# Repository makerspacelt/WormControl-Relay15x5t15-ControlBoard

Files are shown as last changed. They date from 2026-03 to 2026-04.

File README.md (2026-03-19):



---
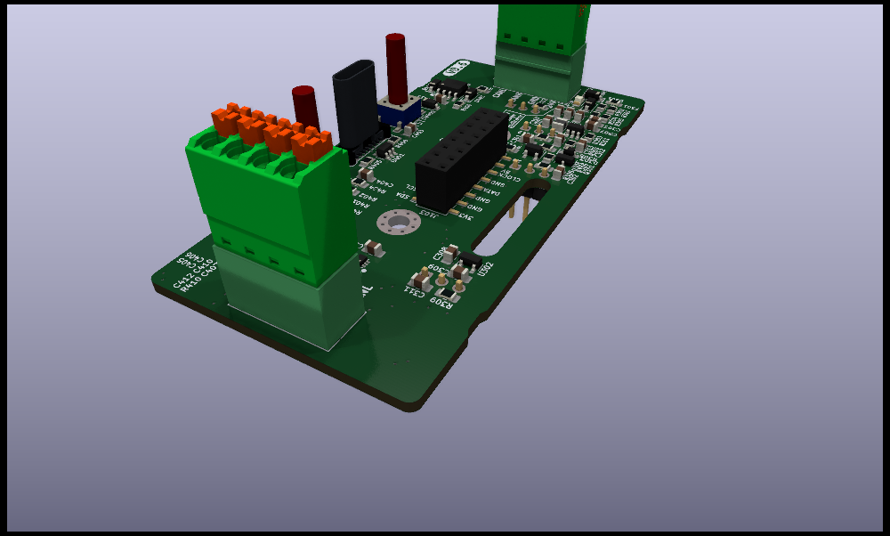
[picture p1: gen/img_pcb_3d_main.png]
PCB 3d main


WormControl Relay Control boards

Dev NOTE: before commit, run `./kibot.sh` to regenerate documentation, bom, gerbers and other assets.

* [schematics.pdf](gen/schematics.pdf)
* [pcb.pdf with dimensions](gen/pcb.pdf)
* [ibom.html](gen/single/ibom.html)

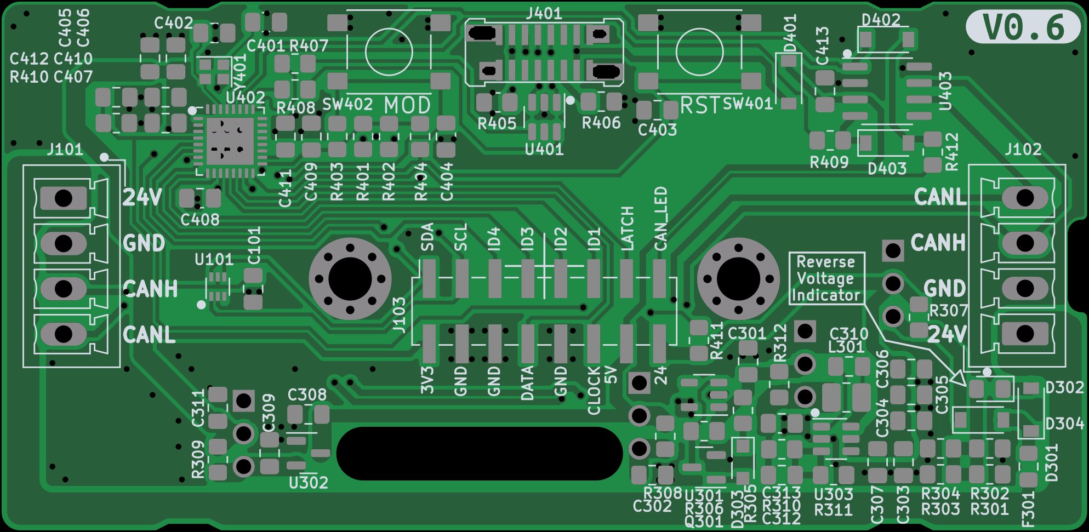
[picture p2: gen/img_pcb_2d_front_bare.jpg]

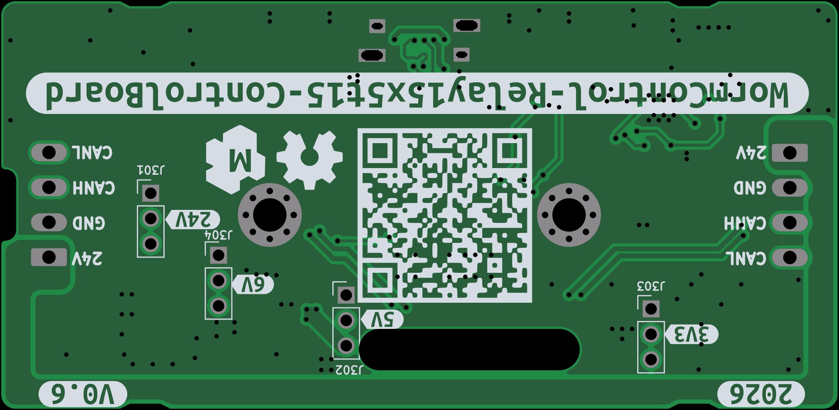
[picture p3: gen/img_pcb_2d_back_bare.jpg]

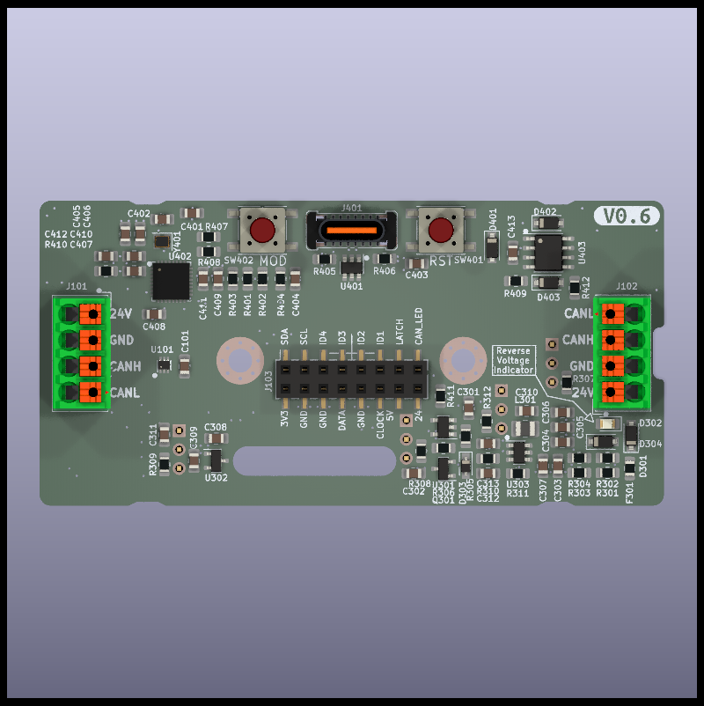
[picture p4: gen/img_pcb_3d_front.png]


---

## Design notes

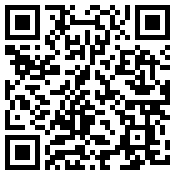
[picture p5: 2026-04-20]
gen/qr_link.png

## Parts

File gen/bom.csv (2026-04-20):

Row | Description | Part | References | Value | Footprint | Quantity Per PCB | Status | Datasheet | lcsc# | jlc-part-type | alt#
1 | Heatsink | Heatsink | BOM101,BOM102 | 1x4 screw plug |  | 2 |  | https://www.lcsc.com/datasheet/lcsc_datasheet_2309070925_DEGSON-15EDGKN-3-5-04P-14-00A-H_C7603442.pdf | C7603442 | E
2 | Unpolarized capacitor | C | C401,C402 | 10p | C_0805_2012Metric_Pad1.18x1.45mm_HandSolder | 2 |  | https://www.lcsc.com/datasheet/lcsc_datasheet_2304140030_Samsung-Electro-Mechanics-CL10C100JB8NNNC_C1634.pdf | C1634 | B
3 | Unpolarized capacitor | C | C312 | 100p | C_0805_2012Metric_Pad1.18x1.45mm_HandSolder | 1 |  | https://www.lcsc.com/datasheet/lcsc_datasheet_2304140030_Samsung-Electro-Mechanics-CL21C101JBANNNC_C1790.pdf | C1790 | B
4 | Unpolarized capacitor | C | C101,C307,C310,C403,C404,C407,C408,C409,C410,C411,C412,C413 | 100n | C_0805_2012Metric_Pad1.18x1.45mm_HandSolder | 12 |  | https://www.lcsc.com/datasheet/lcsc_datasheet_2304140030_Samsung-Electro-Mechanics-CL21B104KCFNNNE_C28233.pdf | C28233 | B
5 | Unpolarized capacitor | C | C406 | 1u | C_0805_2012Metric_Pad1.18x1.45mm_HandSolder | 1 |  | https://www.lcsc.com/datasheet/lcsc_datasheet_2304140030_Samsung-Electro-Mechanics-CL21B105KBFNNNE_C28323.pdf | C28323 | B
6 | Unpolarized capacitor | C | C301,C303,C304,C305,C306,C313 | 10u/50v | C_0805_2012Metric_Pad1.18x1.45mm_HandSolder | 6 |  | https://www.lcsc.com/datasheet/lcsc_datasheet_2411041759_Murata-Electronics-GRM21BR61H106KE43L_C440198.pdf | C440198 | B
7 | Unpolarized capacitor | C | C302,C308,C405 | 22u/25v | C_0805_2012Metric_Pad1.18x1.45mm_HandSolder | 3 |  | https://www.lcsc.com/datasheet/lcsc_datasheet_2304140030_Samsung-Electro-Mechanics-CL21A226MAQNNNE_C45783.pdf | C45783 | B
8 | Unpolarized capacitor | C | C309,C311 | 47u/6V3 | C_0805_2012Metric_Pad1.18x1.45mm_HandSolder | 2 |  | https://www.lcsc.com/datasheet/lcsc_datasheet_2304140030_Samsung-Electro-Mechanics-CL21A226MAQNNNE_C45783.pdf | C16780 | B
9 | Zener diode | D_Zener | D303 | 6V8 | D_SOD-323_HandSoldering | 1 |  | https://www.lcsc.com/datasheet/C123062.pdf | C123062 | E
10 | Schottky diode | D_Schottky | D301,D304,D401,D402,D403 | B5819W | D_SOD-123 | 5 |  | https://www.lcsc.com/datasheet/lcsc_datasheet_2304140030_Jiangsu-Changjing-Electronics-Technology-Co---Ltd--B5819W-SL_C8598.pdf | C8598 | B
11 | Light emitting diode | LED | D302 | BLUE | LED_0805_2012Metric_Pad1.15x1.40mm_HandSolder | 1 |  | https://jlcpcb.com/api/file/downloadByFileSystemAccessId/8550724011370958848 | C2297 | B
12 | Resettable fuse, polymeric positive temperature coefficient | Polyfuse | F301 | 250mA | Fuse_0805_2012Metric_Pad1.15x1.40mm_HandSolder | 1 |  | https://wmsc.lcsc.com/wmsc/upload/file/pdf/v2/lcsc/2404081622_BHFUSE-BSMD0805-025-33V_C22378353.pdf | C22378353 | E
13 | Generic connector, single row, 01x03, script generated (kicad-library-utils/schlib/autogen/connector/) | Conn_01x03 | J301,J302,J303,J304 | 24V | PinHeader_1x03_P2.54mm_Vertical | 4 |  | ~ |  | -
14 | Generic screw terminal, single row, 01x04, script generated (kicad-library-utils/schlib/autogen/connector/) | Screw_Terminal_01x04 | J101,J102 | BUS | PhoenixContact_MCV_1,5_4-G-3.5_1x04_P3.50mm_Vertical | 2 |  | https://www.lcsc.com/datasheet/lcsc_datasheet_2304140030_Ningbo-Xinlaiya-Elec--XY2500V-F-3-5-4P_C880556.pdf | C880556 | E
15 | Generic connector, single row, 01x16, script generated (kicad-library-utils/schlib/autogen/connector/) | Conn_01x16 | J103 | Back | PinSocket_2x08_P2.54mm_Vertical_SMD | 1 |  | https://wmsc.lcsc.com/wmsc/upload/file/pdf/v2/lcsc/2306091018_HCTL-PM254-2-08-S-8-5_C3975153.pdf | C3975153 | E
16 | USB 2.0-only Type-C Receptacle connector | USB_C_Receptacle_USB2.0 | J401 | USB_C_Receptacle_USB2.0 | USB_C_Receptacle_G-Switch_GT-USB-7082G | 1 |  | https://www.lcsc.com/datasheet/lcsc_datasheet_2405271642_G-Switch-GT-USB-7082G_C22383836.pdf | C22383836 | E
17 | Inductor | L | L301 | 3.3uH | L_1008_2520Metric_Pad1.43x2.20mm_HandSolder | 1 |  | https://www.lcsc.com/datasheet/C5832373.pdf | C5832373 | E
18 | NPN transistor, base/emitter/collector | Q_NPN_BEC | Q301 | MMBT3904 | SOT-23 | 1 |  | https://www.lcsc.com/datasheet/C20526.pdf | C20526 | B
19 | Resistor | R | R307,R308,R309,R312 | 0R1 | R_0805_2012Metric_Pad1.20x1.40mm_HandSolder | 4 |  | https://www.lcsc.com/datasheet/lcsc_datasheet_2304140030_UNI-ROYAL-Uniroyal-Elec-0805W8F100LT5E_C127687.pdf | C127687 | E
20 | Resistor | R | R407,R408 | 22R | R_0805_2012Metric_Pad1.20x1.40mm_HandSolder | 2 |  | ~ | C17561 | B
21 | Resistor | R | R301,R302,R303,R304,R401,R402,R403,R404,R405,R406,R409,R410,R412 | 4k7 | R_0805_2012Metric_Pad1.20x1.40mm_HandSolder | 13 |  | ~ | C17673 | B
22 | Resistor | R | R305,R306 | 10k | R_0805_2012Metric_Pad1.20x1.40mm_HandSolder | 2 |  | ~ | C17414 | B
23 | Resistor | R | R311 | 22k | R_0805_2012Metric_Pad1.20x1.40mm_HandSolder | 1 |  | ~ | C17560 | B
24 | Resistor | R | R411 | 150k | R_0805_2012Metric_Pad1.20x1.40mm_HandSolder | 1 |  | ~ | C17470 | B
25 | Resistor | R | R310 | 200k | R_0805_2012Metric_Pad1.20x1.40mm_HandSolder | 1 |  | ~ | C17539 | B
26 | Push button switch, generic, two pins | SW_Push | SW401,SW402 | 15mm | SW_SPST_15 | 2 |  | https://www.lcsc.com/datasheet/lcsc_datasheet_2110120830_XKB-Connection-TS-1102S-C-V-B_C2885154.pdf | C2885154 | E
27 | 300mA Low Dropout Voltage Regulator, Fixed Output 3.3V, SOT-23 | APE8865N-33-HF-3 | U302 | JTD6206-3.3V | SOT-23 | 1 |  | https://www.lcsc.com/datasheet/C42443428.pdf | C5446 | B | C42443428
28 | 300mA Low Dropout Voltage Regulator, Fixed Output 0.9V, SOT-23-5 | TLV71209_SOT23-5 | U301 | LW6550A23E | SOT-23-5 | 1 |  | https://www.lcsc.com/datasheet/C20754712.pdf | C20754712 | E
29 | 1.2 A Simple Buck Regulator, 3-26V input, 1.5Mhz | AOZ1280CI | U303 | ME3121AM6G | SOT-23-6 | 1 |  | https://m.huazhoucn.com/upFiles/common/2022/12/ME3121_Series_E1.0.pdf | C2932938 | E
30 | Digital Temperature Sensor, +/- 3 °C, low-Power, SMBus, 12 bit, Two-Wire Serial Interface, SOT-563 | TMP102xxDRL | U101 | TMP102 | SOT-563 | 1 |  | https://www.ti.com/lit/ds/symlink/tmp102.pdf | C99269 | E
31 | Very low capacitance ESD protection diode, 2 data-line, SOT-23-6 | USBLC6-2SC6 | U401 | USBLC6-2SC6 | SOT-23-6 | 1 |  | https://www.lcsc.com/datasheet/lcsc_datasheet_2311091738_UMW-Youtai-Semiconductor-Co---Ltd--USBLC6-2SC6_C2687116.pdf | C2687116 | E
32 | High-Speed CAN Transceiver, standby mode, split pin, SOIC-8 | TJA1042T | U403 | XL1050 | SOIC-8_3.9x4.9mm_P1.27mm | 1 |  | https://www.lcsc.com/datasheet/lcsc_datasheet_2309141025_XINLUDA-XL1050_C609746.pdf | C609746 | E
33 | esp32-C3FH4X 4MB flash QFN32-1EP 5x5mm EP3.7x3.7mm | esp32-C3FH4X | U402 | esp32-C3FH4X | QFN-32-1EP_5x5mm_P0.5mm_EP3.65x3.65mm | 1 |  | https://www.espressif.com/sites/default/files/documentation/esp32-c3_datasheet_en.pdf | C2858491 | E
34 | Four pin crystal, GND on pins 2 and 4 | Crystal_GND24 | Y401 | 40MHz | Crystal_SMD_2016-4Pin_2.0x1.6mm | 1 |  | https://www.lcsc.com/datasheet/C20885029.pdf | C20885029 | E

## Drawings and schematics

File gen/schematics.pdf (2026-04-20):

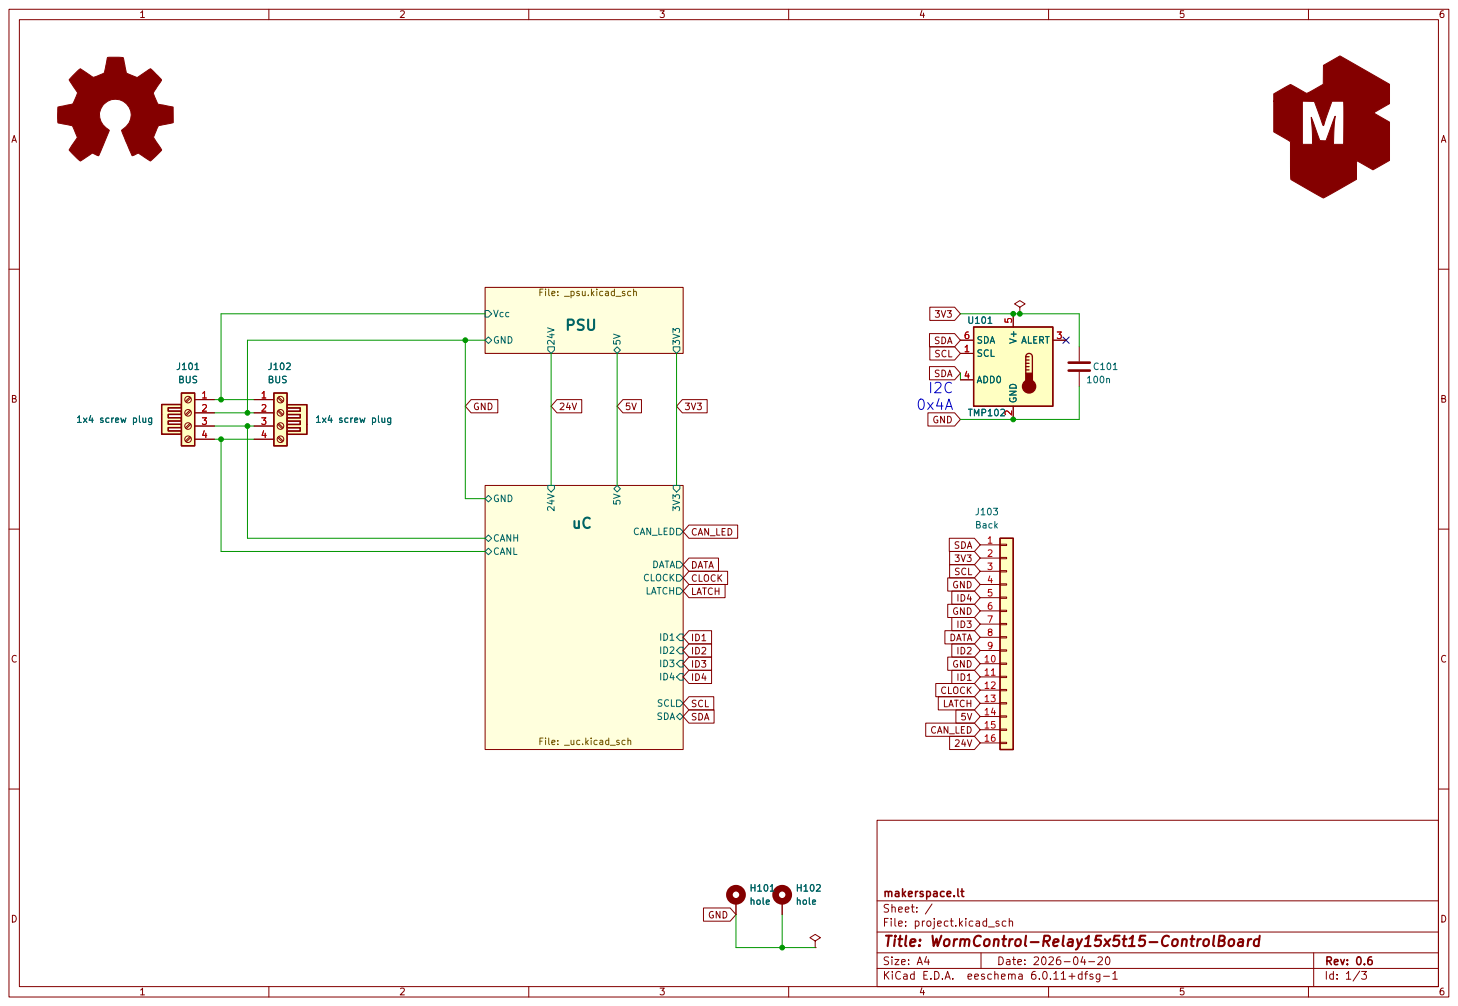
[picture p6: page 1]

Id: 1/3 Title: WormControl-Relay15x5t15-ControlBoard

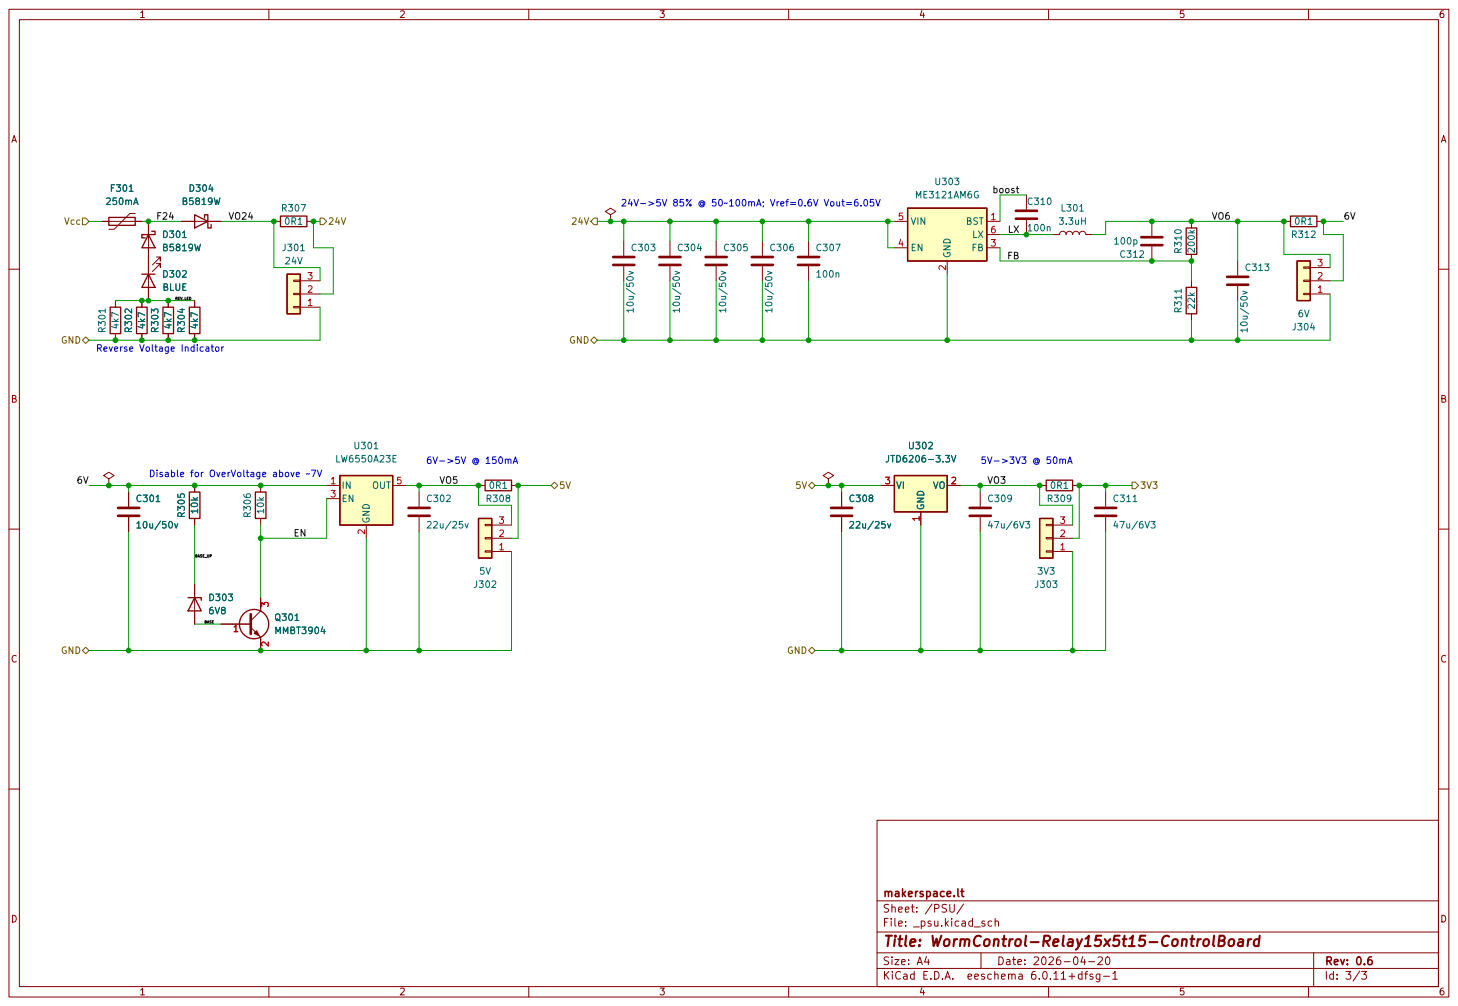
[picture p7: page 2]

boost Disable for OverVoltage above ~7V

Id: 3/3 Title: WormControl-Relay15x5t15-ControlBoard

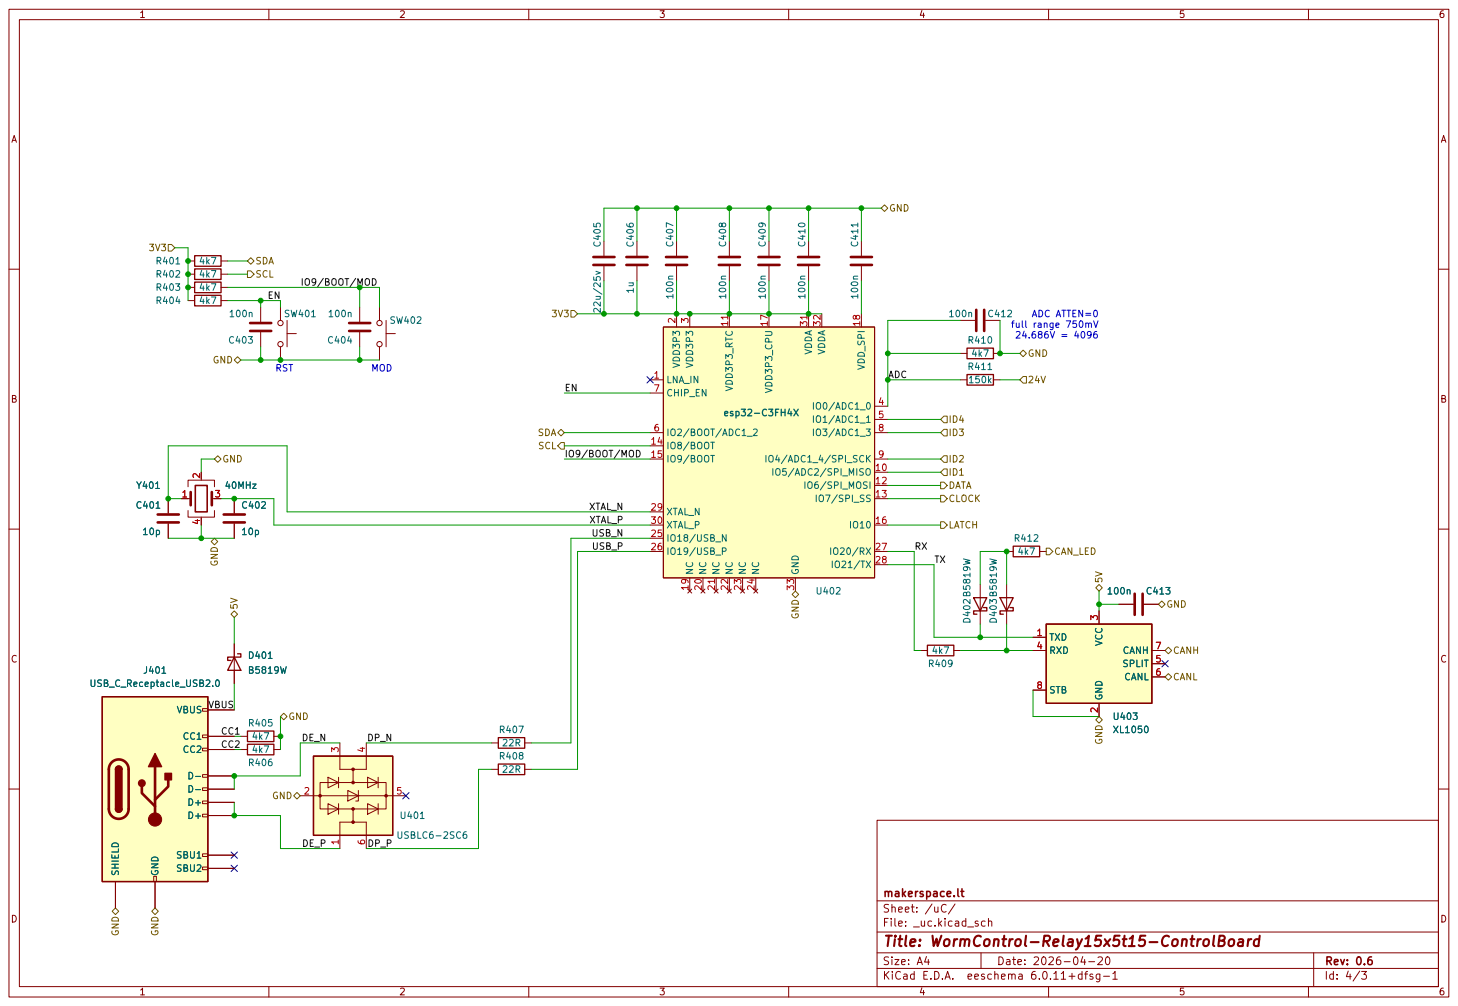
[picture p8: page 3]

File: _uc.kicad_sch Sheet: /uC/ makerspace.lt R407

Id: 4/3 Title: WormControl-Relay15x5t15-ControlBoard

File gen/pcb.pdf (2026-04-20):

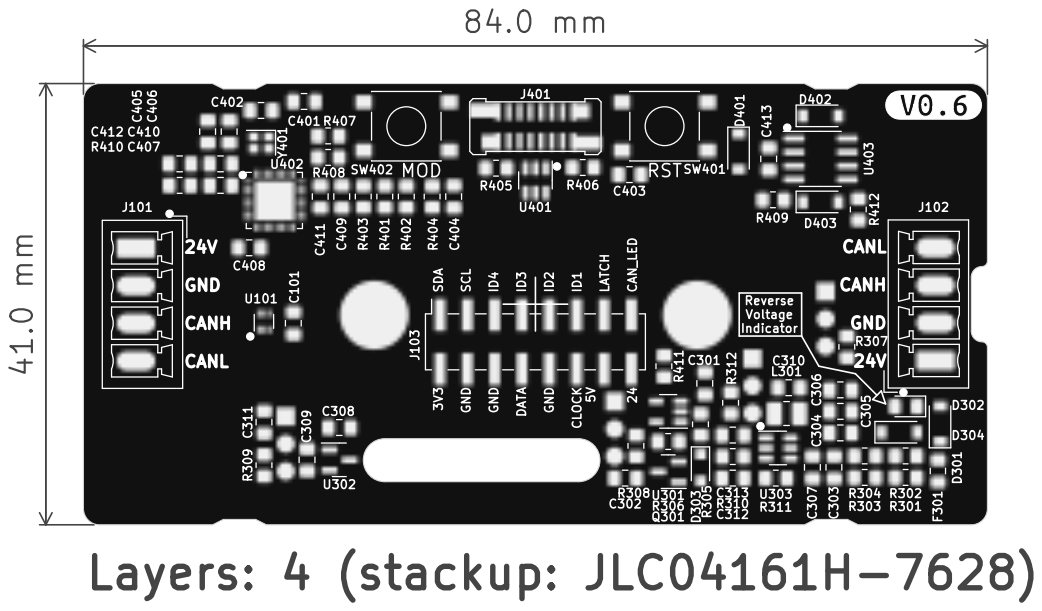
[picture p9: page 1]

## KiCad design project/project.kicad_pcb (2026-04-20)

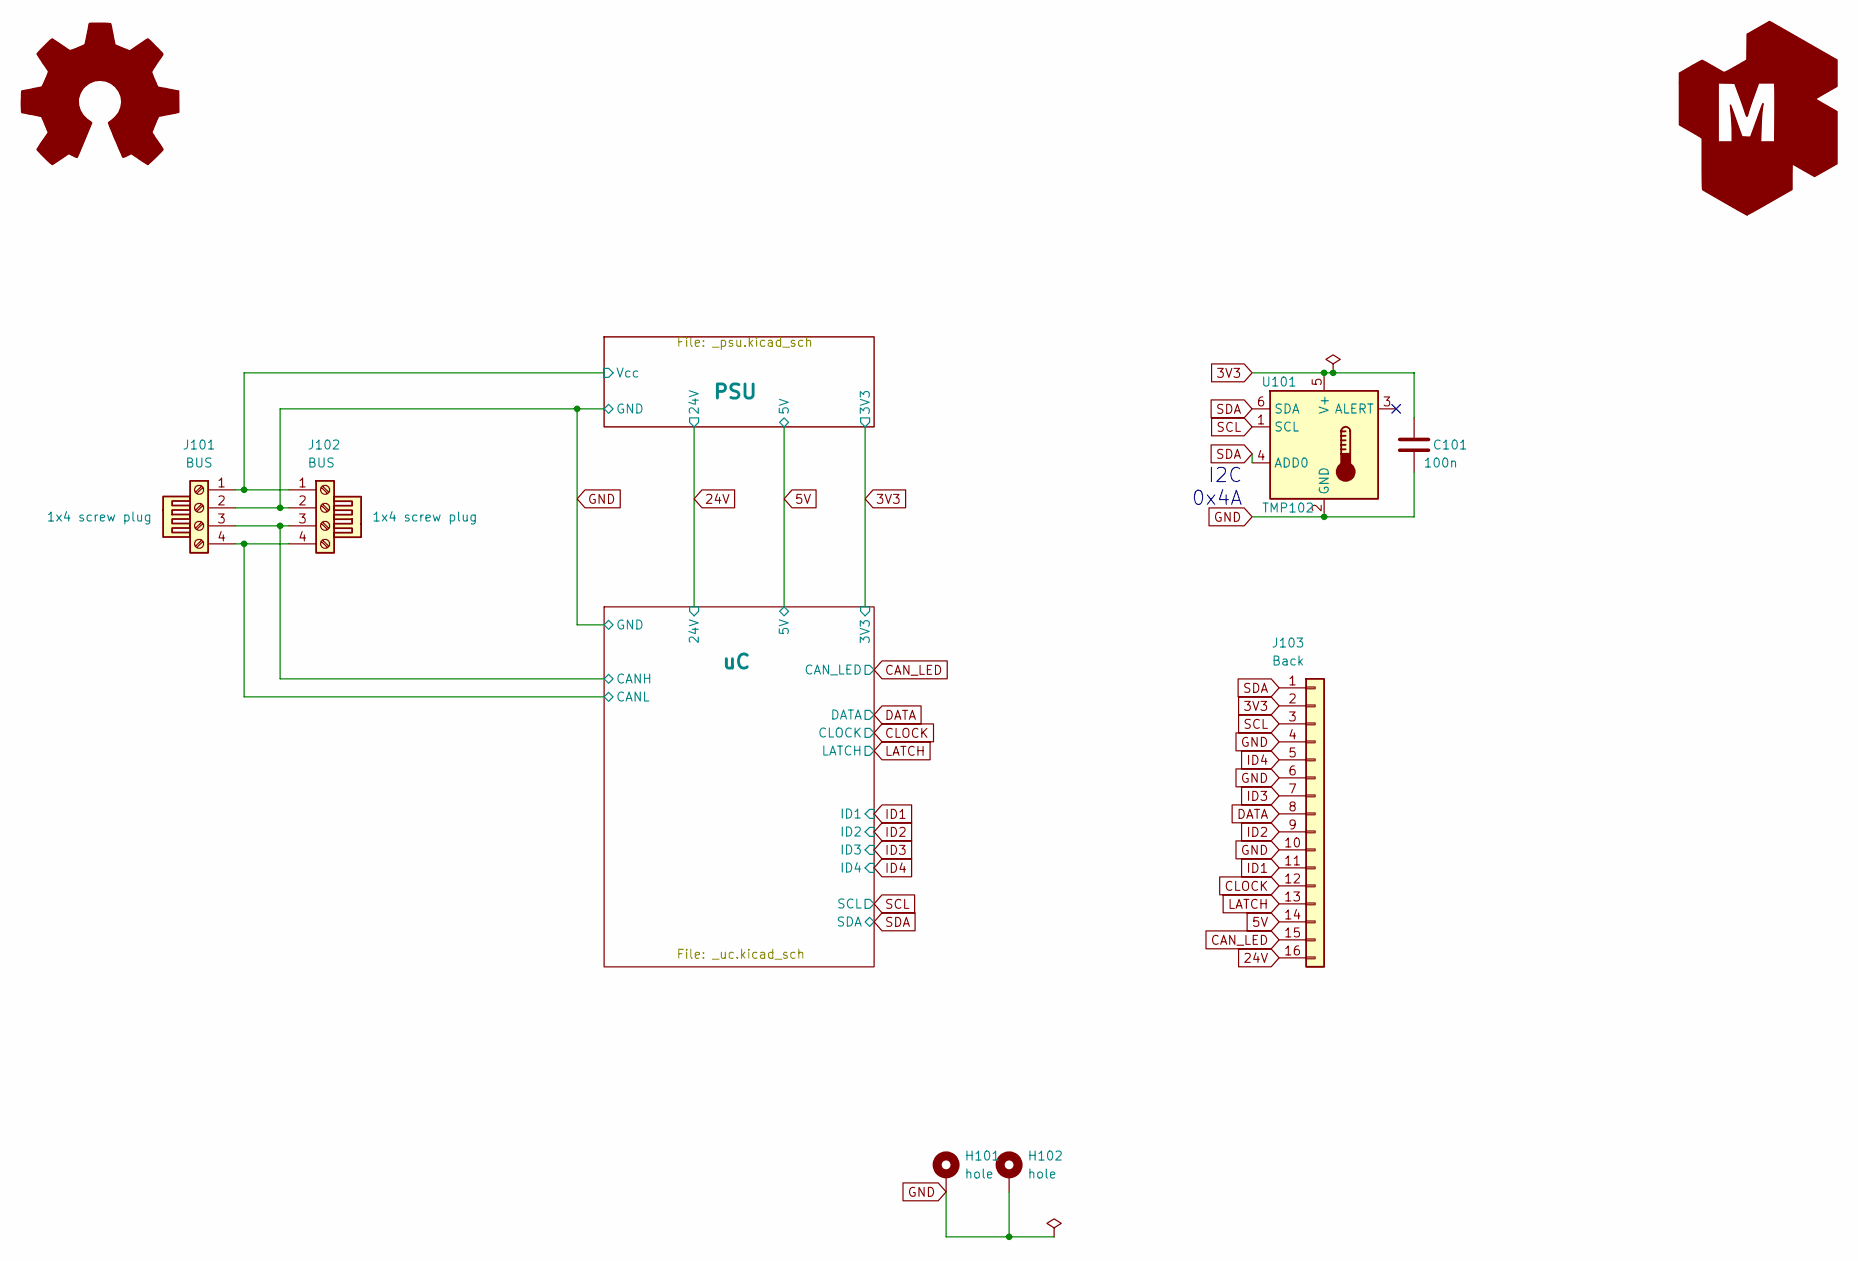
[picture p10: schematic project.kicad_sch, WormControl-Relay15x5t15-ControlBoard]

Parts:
BOM101, BOM102: 1x4 screw plug; jlc-part-type E
C101: 100n; C_0805_2012Metric_Pad1.18x1.45mm_HandSolder; jlc-part-type B
G101: Logo_Open_Hardware_Large; OSHW-Symbol_6.7x6mm_SilkScreen
G102: LOGO_KMS; logo_kms_small_silkscreen
H101, H102: hole; MountingHole_3.2mm_M3_Pad_Via
J101, J102: BUS; PhoenixContact_MCV_1,5_4-G-3.5_1x04_P3.50mm_Vertical; jlc-part-type E
J103: Back; PinSocket_2x08_P2.54mm_Vertical_SMD; lcsc# C3975153
U101: TMP102; SOT-563; jlc-part-type E

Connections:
3V3: C101.1, J103.2, U101.5 (V+); also elsewhere on the board
5V: J103.14; also elsewhere on the board
24V: J103.16; also elsewhere on the board
/PSU/Vcc: J101.1, J102.1; also elsewhere on the board
/uC/CANH: J101.3, J102.3; also elsewhere on the board
/uC/CANL: J101.4, J102.4; also elsewhere on the board
CAN_LED: J103.15; also elsewhere on the board
CLOCK: J103.12; also elsewhere on the board
DATA: J103.8; also elsewhere on the board
GND: C101.2, H101.1, H102.1, J101.2, J102.2, J103.4, J103.6, J103.10, U101.2 (GND); also elsewhere on the board
ID1: J103.11; also elsewhere on the board
ID2: J103.9; also elsewhere on the board
ID3: J103.7; also elsewhere on the board
ID4: J103.5; also elsewhere on the board
LATCH: J103.13; also elsewhere on the board
SCL: J103.3, U101.1 (SCL); also elsewhere on the board
SDA: J103.1, U101.4 (ADD0), U101.6 (SDA); also elsewhere on the board

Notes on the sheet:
I2C 0x4A

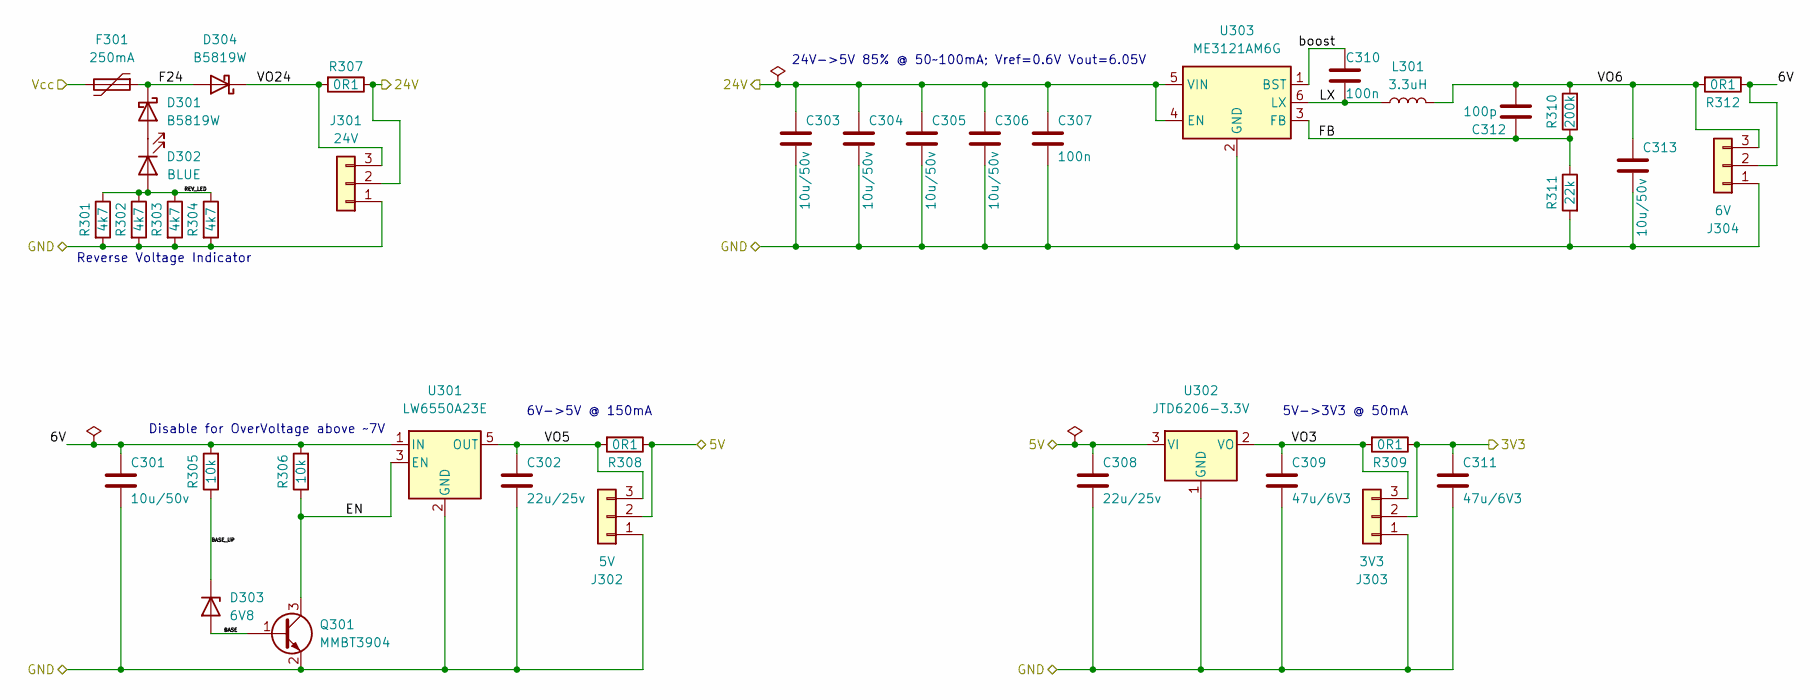
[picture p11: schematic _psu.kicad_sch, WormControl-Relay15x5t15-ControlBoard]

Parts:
C301, C303, C304, C305, C306, C313: 10u/50v; C_0805_2012Metric_Pad1.18x1.45mm_HandSolder; jlc-part-type B
C302, C308: 22u/25v; C_0805_2012Metric_Pad1.18x1.45mm_HandSolder; jlc-part-type B
C307, C310: 100n; C_0805_2012Metric_Pad1.18x1.45mm_HandSolder; jlc-part-type B
C309, C311: 47u/6V3; C_0805_2012Metric_Pad1.18x1.45mm_HandSolder; jlc-part-type B
C312: 100p; C_0805_2012Metric_Pad1.18x1.45mm_HandSolder; jlc-part-type B
D301, D304: B5819W; D_SOD-123; jlc-part-type B
D302: BLUE; LED_0805_2012Metric_Pad1.15x1.40mm_HandSolder; jlc-part-type B
D303: 6V8; D_SOD-323_HandSoldering; jlc-part-type E
F301: 250mA; Fuse_0805_2012Metric_Pad1.15x1.40mm_HandSolder; lcsc# C22378353
J301: 24V; PinHeader_1x03_P2.54mm_Vertical
J302: 5V; PinHeader_1x03_P2.54mm_Vertical
J303: 3V3; PinHeader_1x03_P2.54mm_Vertical
J304: 6V; PinHeader_1x03_P2.54mm_Vertical
L301: 3.3uH; L_1008_2520Metric_Pad1.43x2.20mm_HandSolder; jlc-part-type E
Q301: MMBT3904; SOT-23; jlc-part-type B
R301, R302, R303, R304: 4k7; R_0805_2012Metric_Pad1.20x1.40mm_HandSolder; jlc-part-type B
R305, R306: 10k; R_0805_2012Metric_Pad1.20x1.40mm_HandSolder; jlc-part-type B
R307, R308, R309, R312: 0R1; R_0805_2012Metric_Pad1.20x1.40mm_HandSolder; jlc-part-type E
R310: 200k; R_0805_2012Metric_Pad1.20x1.40mm_HandSolder; jlc-part-type B
R311: 22k; R_0805_2012Metric_Pad1.20x1.40mm_HandSolder; jlc-part-type B
U301: LW6550A23E; SOT-23-5; jlc-part-type E
U302: JTD6206-3.3V; SOT-23; jlc-part-type B
U303: ME3121AM6G; SOT-23-6; jlc-part-type E

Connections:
3V3: C311.1, J303.2, R309.1; also elsewhere on the board
5V: C308.1, J302.2, R308.1, U302.3 (VI); also elsewhere on the board
24V: C303.1, C304.1, C305.1, C306.1, C307.1, J301.2, R307.1, U303.4 (EN), U303.5 (VIN); also elsewhere on the board
/PSU/6V: C301.1, J304.2, R305.2, R306.2, R312.1, U301.1 (IN)
/PSU/BASE: D303.2 (A), Q301.1 (B)
/PSU/BASE_UP: D303.1 (K), R305.1
/PSU/EN: Q301.3 (C), R306.1, U301.3 (EN)
/PSU/F24: D301.1 (K), D304.2 (A), F301.1
/PSU/FB: C312.1, R310.1, R311.1, U303.3 (FB)
/PSU/LX: C310.2, L301.1, U303.6 (LX)
/PSU/REV_LED: D302.2 (A), R301.1, R302.1, R303.1, R304.1
/PSU/VO3: C309.1, J303.3, R309.2, U302.2 (VO)
/PSU/VO5: C302.1, J302.3, R308.2, U301.5 (OUT)
/PSU/VO6: C312.2, C313.1, J304.3, L301.2, R310.2, R312.2
/PSU/VO24: D304.1 (K), J301.3, R307.2
/PSU/Vcc: F301.2; also elsewhere on the board
/PSU/boost: C310.1, U303.1 (BST)
GND: C301.2, C302.2, C303.2, C304.2, C305.2, C306.2, C307.2, C308.2, C309.2, C311.2, C313.2, J301.1, J302.1, J303.1, J304.1, Q301.2 (E), R301.2, R302.2, R303.2, R304.2, R311.2, U301.2 (GND), U302.1 (GND), U303.2 (GND); also elsewhere on the board
unnamed: D301.2 (A), D302.1 (K)

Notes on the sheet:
24V->5V 85% @ 50~100mA; Vref=0.6V Vout=6.05V
5V->3V3 @ 50mA
Reverse Voltage Indicator
6V->5V @ 150mA
Disable for OverVoltage above ~7V

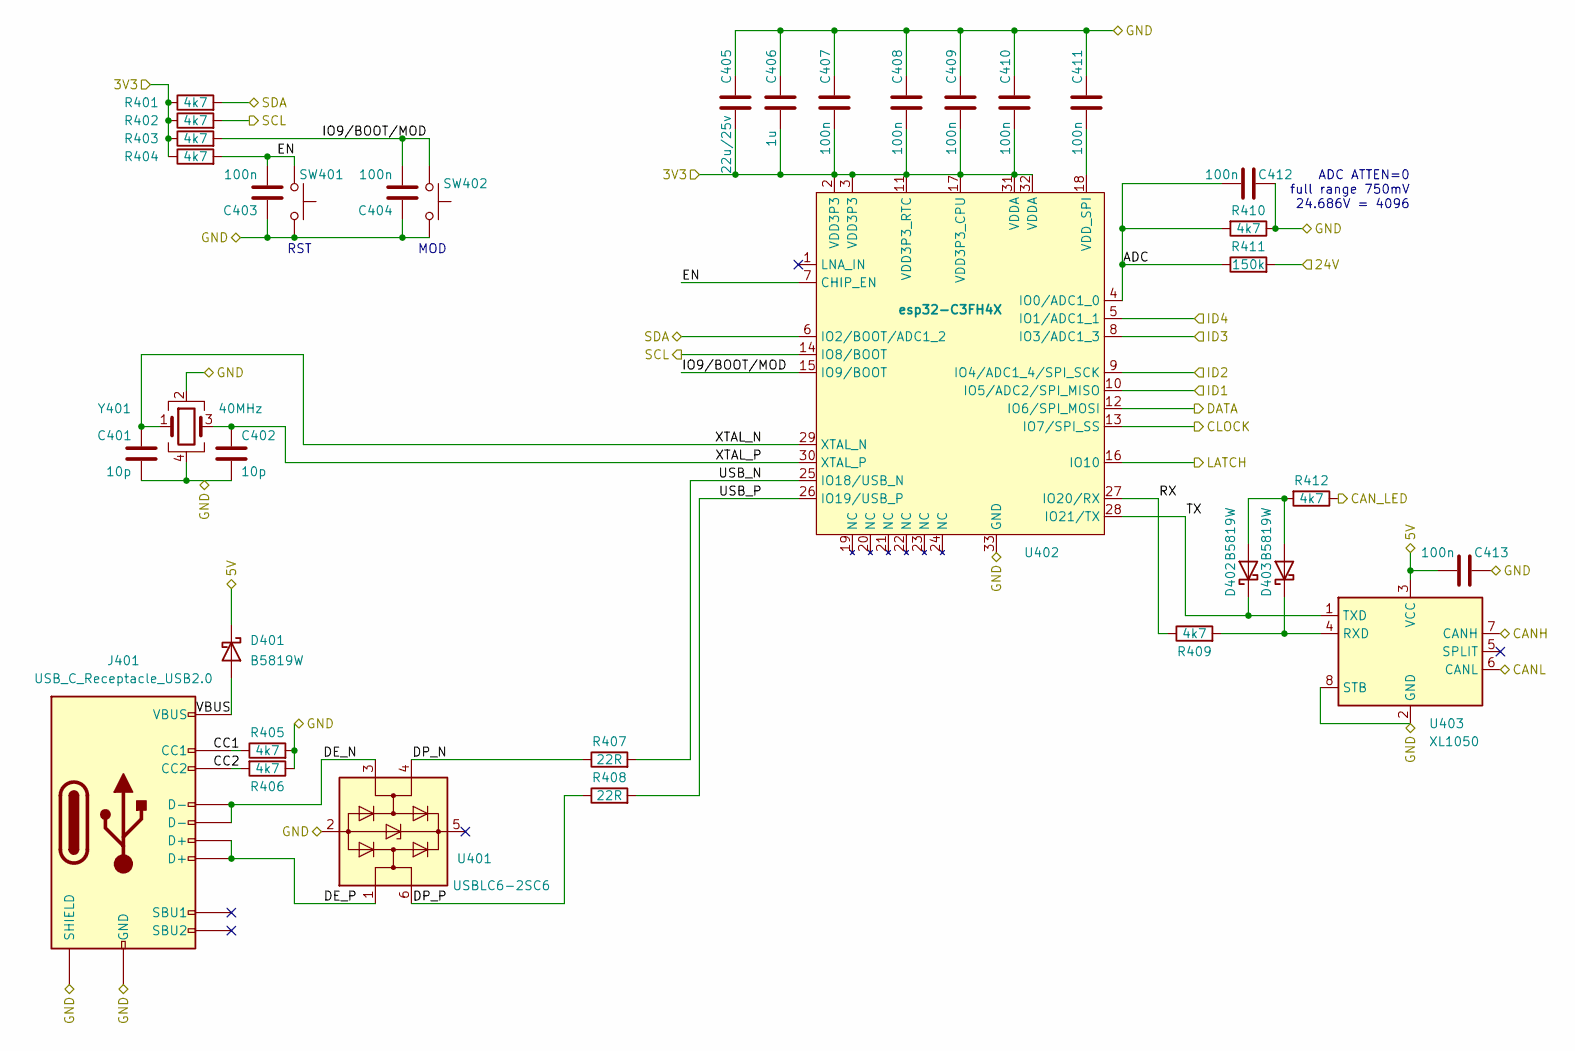
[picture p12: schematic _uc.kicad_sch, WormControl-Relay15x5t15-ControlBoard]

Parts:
C401, C402: 10p; C_0805_2012Metric_Pad1.18x1.45mm_HandSolder; jlc-part-type B
C403, C404, C407, C408, C409, C410, C411, C412, C413: 100n; C_0805_2012Metric_Pad1.18x1.45mm_HandSolder; jlc-part-type B
C405: 22u/25v; C_0805_2012Metric_Pad1.18x1.45mm_HandSolder; jlc-part-type B
C406: 1u; C_0805_2012Metric_Pad1.18x1.45mm_HandSolder; jlc-part-type B
D401, D402, D403: B5819W; D_SOD-123; jlc-part-type B
J401: USB_C_Receptacle_USB2.0; USB_C_Receptacle_G-Switch_GT-USB-7082G; jlc-part-type E
R401, R402, R403, R404, R405, R406, R409, R410, R412: 4k7; R_0805_2012Metric_Pad1.20x1.40mm_HandSolder; jlc-part-type B
R407, R408: 22R; R_0805_2012Metric_Pad1.20x1.40mm_HandSolder; jlc-part-type B
R411: 150k; R_0805_2012Metric_Pad1.20x1.40mm_HandSolder; jlc-part-type B
SW401, SW402: 15mm; SW_SPST_15; jlc-part-type E
U401: USBLC6-2SC6; SOT-23-6; jlc-part-type E
U402: esp32-C3FH4X; QFN-32-1EP_5x5mm_P0.5mm_EP3.65x3.65mm; jlc-part-type E
U403: XL1050; SOIC-8_3.9x4.9mm_P1.27mm; jlc-part-type E
Y401: 40MHz; Crystal_SMD_2016-4Pin_2.0x1.6mm; jlc-part-type E

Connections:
3V3: C405.2, C406.2, C407.1, C408.1, C409.1, C410.1, R401.1, R402.1, R403.1, R404.1, U402.2 (VDD3P3), U402.3 (VDD3P3), U402.11 (VDD3P3_RTC), U402.17 (VDD3P3_CPU), U402.31 (VDDA), U402.32 (VDDA); also elsewhere on the board
5V: C413.1, D401.1 (K), U403.3 (VCC); also elsewhere on the board
24V: R411.2; also elsewhere on the board
/uC/ADC: C412.1, R410.2, R411.1, U402.4 (IO0/ADC1_0)
/uC/CANH: U403.7 (CANH); also elsewhere on the board
/uC/CANL: U403.6 (CANL); also elsewhere on the board
/uC/CC1: J401.A5 (CC1), R405.1
/uC/CC2: J401.B5 (CC2), R406.2
/uC/DE_N: J401.A7 (D-), J401.B7 (D-), U401.3 (I/O2)
/uC/DE_P: J401.A6 (D+), J401.B6 (D+), U401.1 (I/O1)
/uC/DP_N: R407.1, U401.4 (I/O2)
/uC/DP_P: R408.1, U401.6 (I/O1)
/uC/EN: C403.2, R404.2, SW401.1, U402.7 (CHIP_EN)
/uC/IO9/BOOT/MOD: C404.2, R403.2, SW402.1, U402.15 (IO9/BOOT)
/uC/RX: R409.1, U402.27 (IO20/RX)
/uC/TX: D402.1 (K), U402.28 (IO21/TX), U403.1 (TXD)
/uC/USB_N: R407.2, U402.25 (IO18/USB_N)
/uC/USB_P: R408.2, U402.26 (IO19/USB_P)
/uC/VBUS: D401.2 (A), J401.A4 (VBUS), J401.A9 (VBUS), J401.B4 (VBUS), J401.B9 (VBUS)
/uC/XTAL_N: C401.1, U402.29 (XTAL_N), Y401.1
/uC/XTAL_P: C402.1, U402.30 (XTAL_P), Y401.3
CAN_LED: R412.1; also elsewhere on the board
CLOCK: U402.13 (IO7/SPI_SS); also elsewhere on the board
DATA: U402.12 (IO6/SPI_MOSI); also elsewhere on the board
GND: C401.2, C402.2, C403.1, C404.1, C405.1, C406.1, C407.2, C408.2, C409.2, C410.2, C411.2, C412.2, C413.2, J401.A1 (GND), J401.A12 (GND), J401.B1 (GND), J401.B12 (GND), J401.S1 (SHIELD), R405.2, R406.1, R410.1, SW401.2, SW402.2, U401.2 (GND), U402.33 (GND), U403.2 (GND), U403.8 (STB), Y401.2, Y401.4; also elsewhere on the board
ID1: U402.10 (IO5/ADC2/SPI_MISO); also elsewhere on the board
ID2: U402.9 (IO4/ADC1_4/SPI_SCK); also elsewhere on the board
ID3: U402.8 (IO3/ADC1_3); also elsewhere on the board
ID4: U402.5 (IO1/ADC1_1); also elsewhere on the board
LATCH: U402.16 (IO10); also elsewhere on the board
unnamed: C411.1, U402.18 (VDD_SPI)
unnamed: D402.2 (A), D403.2 (A), R412.2
unnamed: D403.1 (K), R409.2, U403.4 (RXD)
SCL: R402.2, U402.14 (IO8/BOOT); also elsewhere on the board
SDA: R401.2, U402.6 (IO2/BOOT/ADC1_2); also elsewhere on the board

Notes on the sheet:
RST
ADC ATTEN=0 full range 750mV 24.686V = 4096
MOD

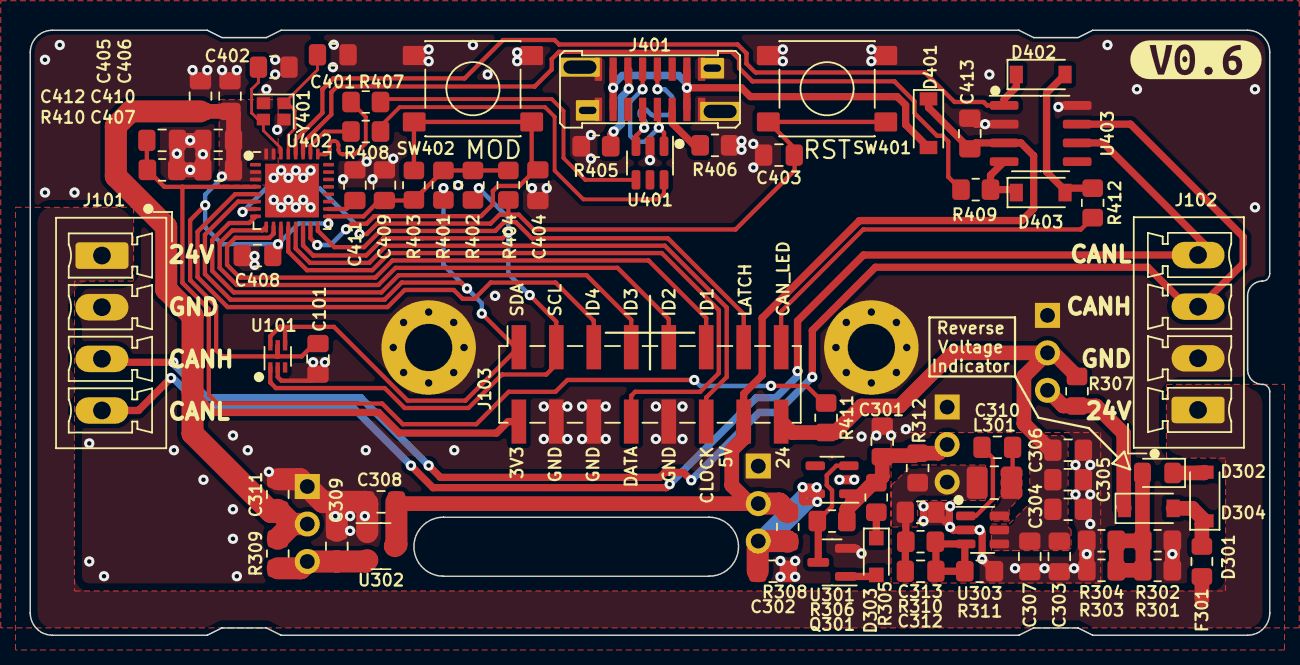
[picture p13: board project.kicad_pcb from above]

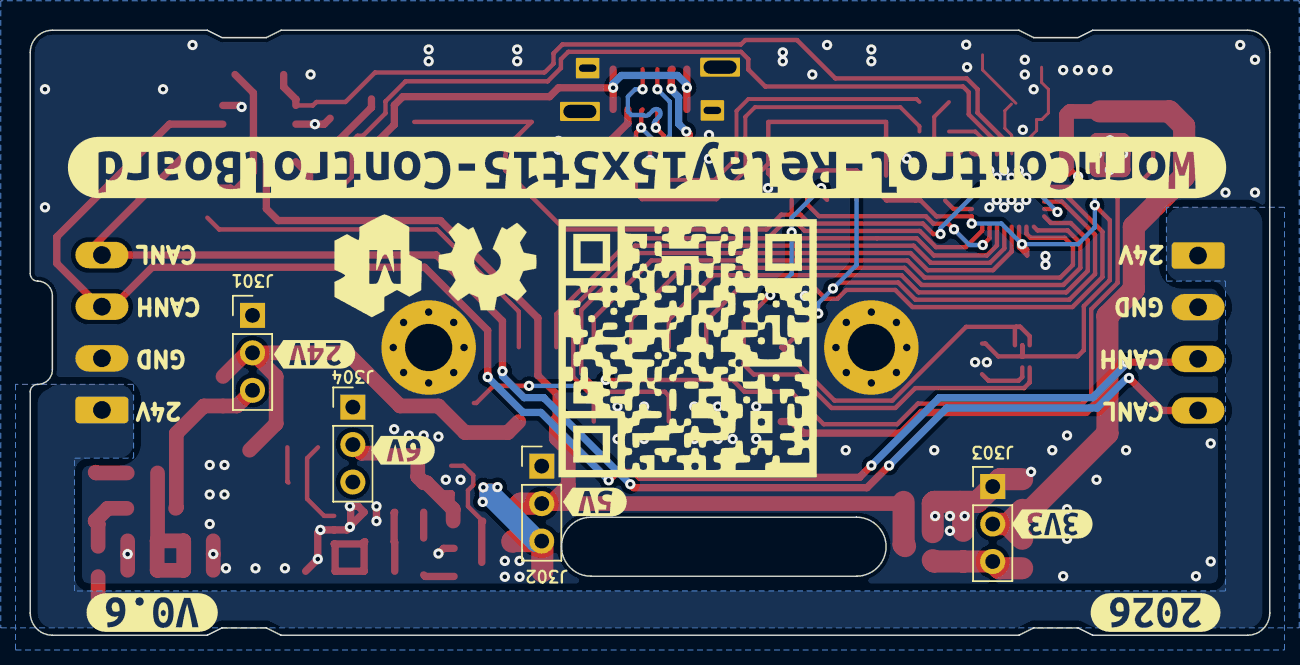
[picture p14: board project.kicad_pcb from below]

Board: 4 copper layers, 84.0 x 41.0 mm, 91 parts (13 on the bottom side), 50 nets.

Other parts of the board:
kibuzzard-68F6C7D9: G***; kibuzzard-68F6C7D9
kibuzzard-68F6C8CD: G***; kibuzzard-68F6C8CD
kibuzzard-68F6C776: G***; kibuzzard-68F6C776
kibuzzard-68F6C793: G***; kibuzzard-68F6C793
kibuzzard-69BC0AB9: G***; kibuzzard-69BC0AB9
kibuzzard-69BC0BA6: G***; kibuzzard-69BC0BA6
kibuzzard-69E60A07: G***; kibuzzard-69E60A07
kibuzzard-69E609FA: G***; kibuzzard-69E609FA

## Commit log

2026-03-19 spritting up boards into separate repos
    [_bom.csv, _driver.kicad_sch, _psu.kicad_sch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]
2026-03-19 part consolidation and QoL improvements
    * Using same crystal as in other projects
    * Switching to TMP102 as TMP101 is no longer available
    * Adding cutouts to make assembly esier
    * Making net names more readable
    * bumping up version
    [_bom.csv, _psu.kicad_sch, _uc.kicad_sch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]
2026-03-19 adding cutout for easier assembly
    [project--NPTH_map.gbr, project--PTH_map.gbr, project-B_Cu.gbl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]
2026-04-20 fixing tmp102 pinout
    [_psu.kicad_sch, _uc.kicad_sch, bom.csv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]
